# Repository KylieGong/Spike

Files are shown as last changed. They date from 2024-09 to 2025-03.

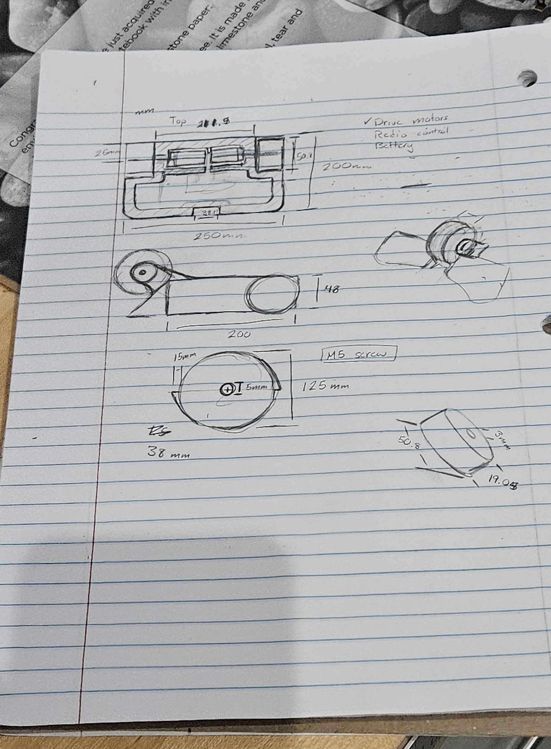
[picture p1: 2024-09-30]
Sketches/dim_drawings.jpg

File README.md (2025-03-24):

# Spike
Spike is a 1lb combat robot designed to participate at the competition known 
as 

**SCR@M**: https://leatherbacks.notion.site/SCR-M-Allowed-Parts-List-7415e14e8c94436496a05054f4add28d

This event was organized by the combat robotics club **Leatherbacks Combat Robotics** 

Instagram profile: https://www.instagram.com/leatherbacks.umd/

## Type of robot
Spike is a vertical spinner robot with two teeths and guards attached to the front so it can break in half whoever stands in its way. 
It's body structure was made of PLA with about 15% in-fill on average.

## Part List
See document attached bill of materials.csv

## CAD Design 
The software used was Solidworks 2024 Student Edition
### First Version


### Spike last version


## Ready before fight


## Fight!



https://photos.app.goo.gl/Wb8rTZ4aMuBoXnDs7

## After fight 


## Future improvements 
- Change the way the weapon mounts are attached.
- Determine a better attack angle for the spinner.
- Check zones that can be reduced without pushing the electrical wiring and components inside. 
- Try new ideas for fastening.
- Design a different geometry for the saw.

## Lessons Learned
- Tolerances are crucial to achieve some design requirements. 
- Measure every component if available so less corrections are required.
- Look for the simple ways to fasten and assembly together components. 
- In real there's always fixes on  we can do at the cost of performance (eg: plastic welding)

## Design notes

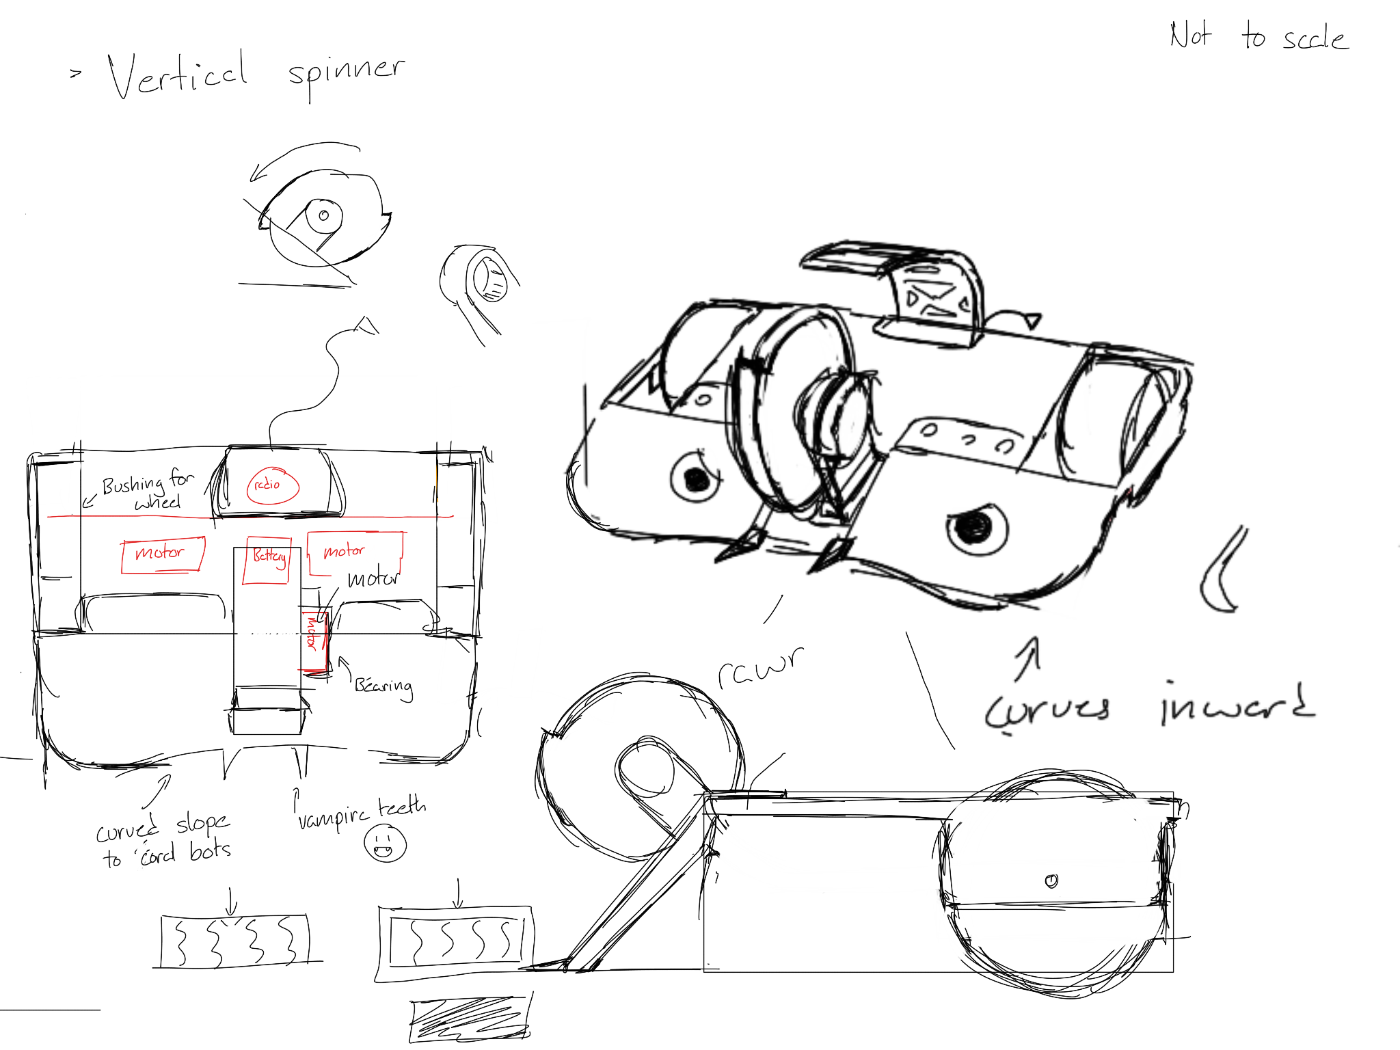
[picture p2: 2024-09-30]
Sketches/design.png

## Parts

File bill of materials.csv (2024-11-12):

ITEM NO. | PART NUMBER | DESCRIPTION | LINK | QTY.
1 | chassie v4 | Body spike | N/A | 1
2 | motor drive mount | PLA | N/A | 2
3 | cover plate | PLA | N/A | 1
4 | weapon mini | PLA 100% infill | N/A | 1
5 | weapon mount 1 | PLA | N/A | 1
6 | weapon mount 2 | PLA | N/A | 1
7 | teeth armor | PLA | N/A | 1
8 | wheels | 2x0.75in foam wheels | https://www.fingertechrobotics.com/proddetail.php?prod=ft-foam-wheels | 2
9 | battery with cables | Gaoneng GNB 11.4V 3S 380mAh 90C LiHV Micro Battery - XT30 | https://www.racedayquads.com/products/gaoneng-gnb-11-4v-3s-380mah-90c-lihv-micro-battery-xt30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 | 1
10 | FingerTech_Silver_Spark_11 | 16mm shaft | https://www.fingertechrobotics.com/proddetail.php?prod=ft-Sspark16 | 2
11 | Lite_Hub | Lite hubs for wheels | https://www.fingertechrobotics.com/proddetail.php?prod=ft-lite-hubs | 2
12 | mini power switch | Fingertech mini power switch | https://www.fingertechrobotics.com/proddetail.php?prod=ft-mini-switch | 1
13 | ESC Motor drive | Budget Ant DESC | https://repeat-robotics.com/buy/desc/ | 2
14 | ESC weapon | Flycolor Raptor 5 BLHeli_32 3-6S DShot 1200 35A ESC | https://www.getfpv.com/flycolor-x-cross-blheli-32-35a-3-6s-dshot-1200-esc.html | 1
15 | Radiomaster R84 | ER4 2.4GHz ELRS PWM Receiver | https://www.radiomasterrc.com/products/er4-2-4ghz-elrs-pwm-receiver | 1
16 | 2207 motor | TMOTOR Velox V2207 V3 Brushless Drone Motor | https://shop.tmotor.com/products/tmotor-velox-v2207-v3-motor | 1
17 | 5972K197 | Ball Bearing 5mm | https://www.mcmaster.com/products/bearings/ball-bearings~/ball-bearings-8/shaft-diameter~5-mm/ | 1
18 | 91290A115 | Alloy Steel Socket Head Screw | https://www.mcmaster.com/catalog/130/3544/91290A115 | 12
19 | 91290A117 | Alloy Steel Socket Head Screw | https://www.mcmaster.com/catalog/130/3544/91290A119 | 4
20 | 91290A123 | Alloy Steel Socket Head Screw | https://www.mcmaster.com/catalog/130/3544/91290A123 | 4
21 | 2-56 Button head screws | Button Socket Cap Screw: #2-56 3/16" Length Under Head Alloy Steel Black Oxide | https://www.fingertechrobotics.com/proddetail.php?prod=screw256BH-25pcs | 4
22 | Head inserts | Brass Tapping Inserts for Plastic | https://www.amazon.com/Threaded-Inserts-Printing-Embedment-Automotive/dp/B0BQJ6CRNJ | 16

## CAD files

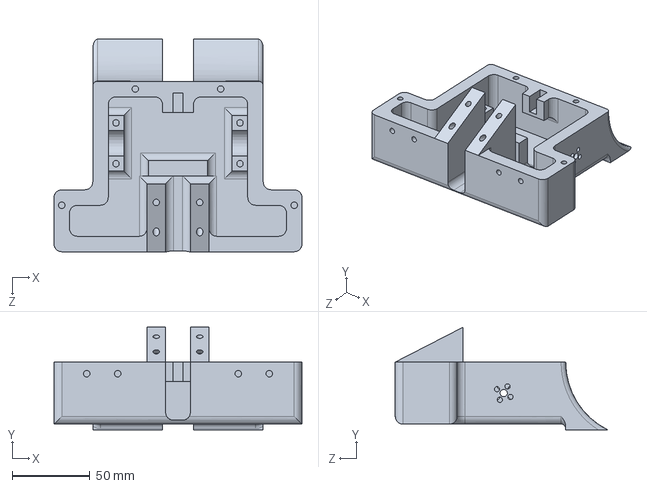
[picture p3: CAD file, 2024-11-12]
CAD/chassis_v4.SLDPRT
160.0 x 66.2 x 137.1 mm

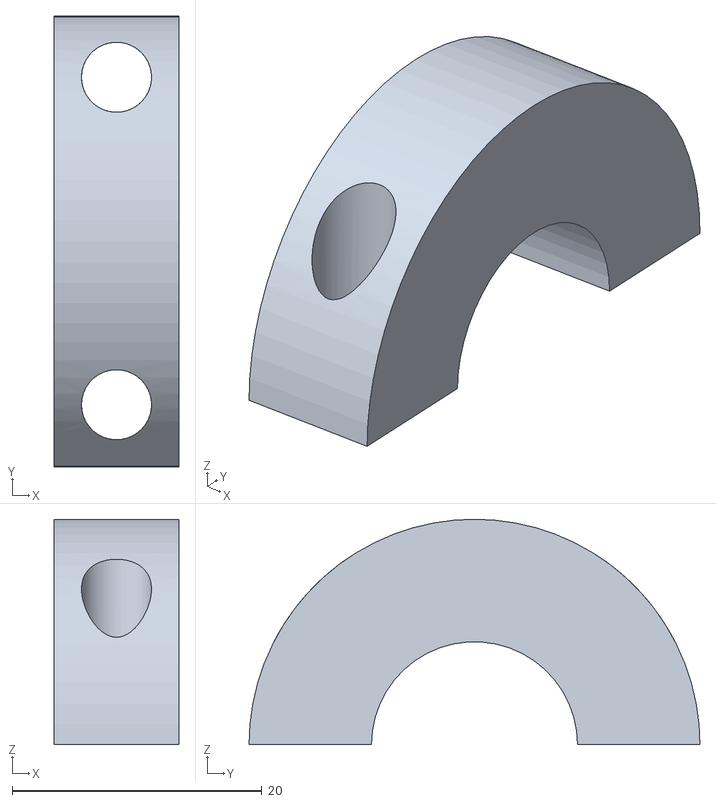
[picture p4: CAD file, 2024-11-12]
Parts to print/motor drive mount up-PLA-2X.STL
10.0 x 36.1 x 18.0

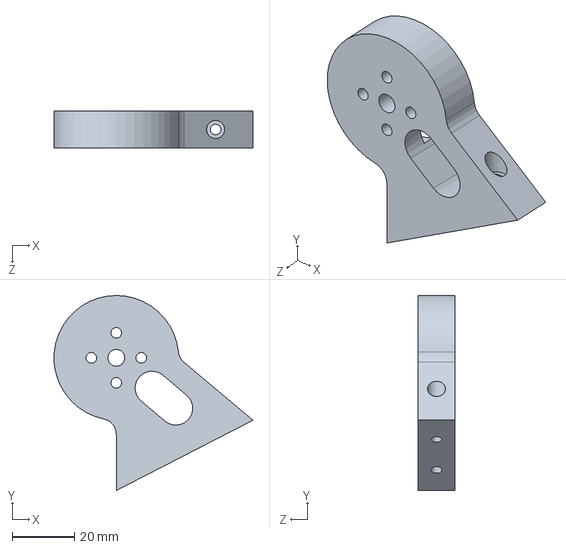
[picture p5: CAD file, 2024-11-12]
CAD/mount for weapon part1.SLDPRT
63.8 x 62.5 x 12.0 mm

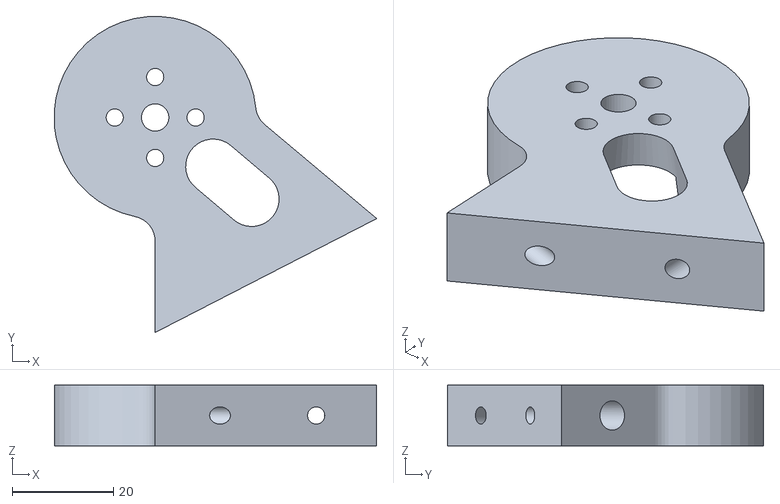
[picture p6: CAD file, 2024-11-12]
Parts to print/mount weapon1-PLA-1X.STL
63.8 x 62.5 x 12.0

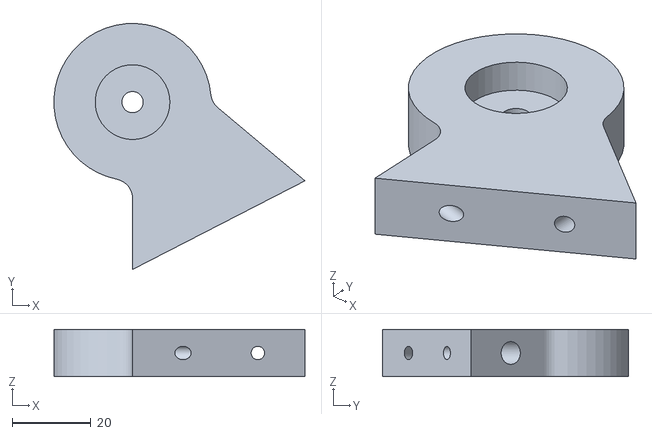
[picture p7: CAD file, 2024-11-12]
Parts to print/mount weapon2-PLA-1X.STL
63.8 x 62.5 x 12.0

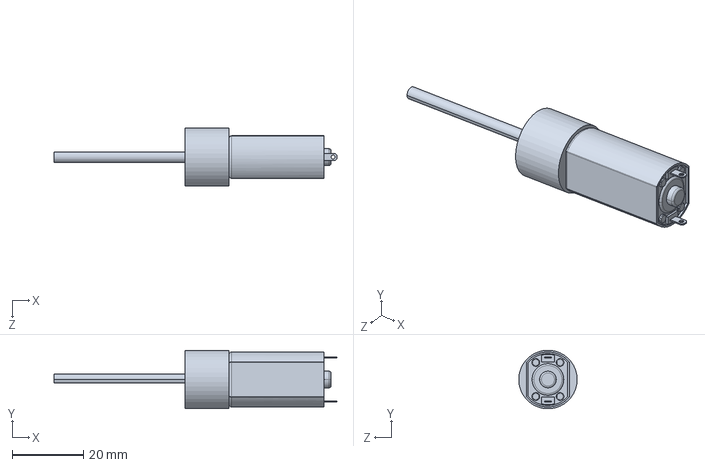
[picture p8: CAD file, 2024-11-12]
CAD/FingerTech_Silver_Spark_223350.SLDPRT
79.7 x 16.5 x 16.5 mm

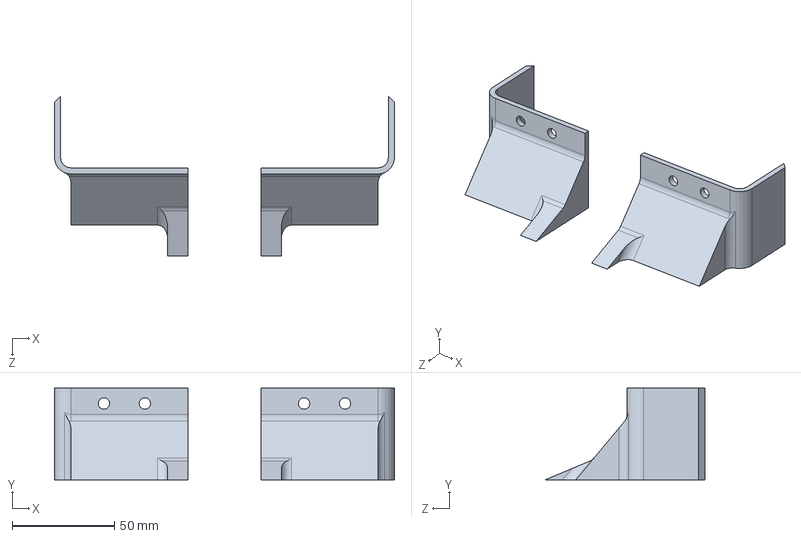
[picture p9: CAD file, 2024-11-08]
CAD/wedge teeth.SLDPRT
166.0 x 44.8 x 78.0 mm

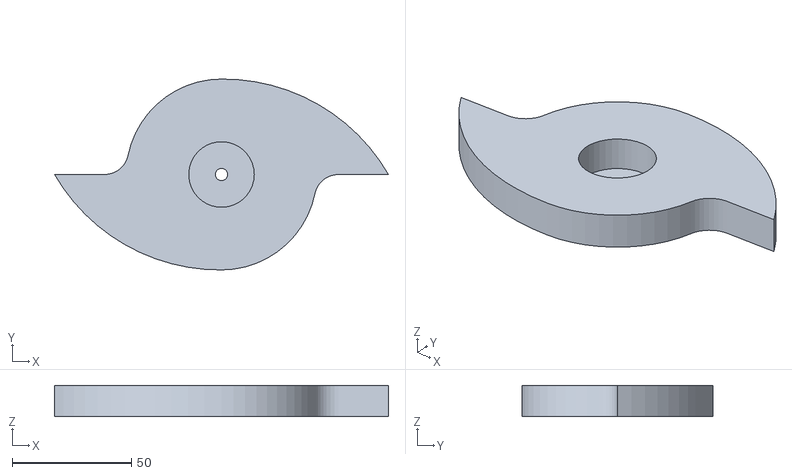
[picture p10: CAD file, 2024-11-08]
Parts to print/weapon-PLA-1X-100% infill.STL
140.0 x 80.0 x 13.0

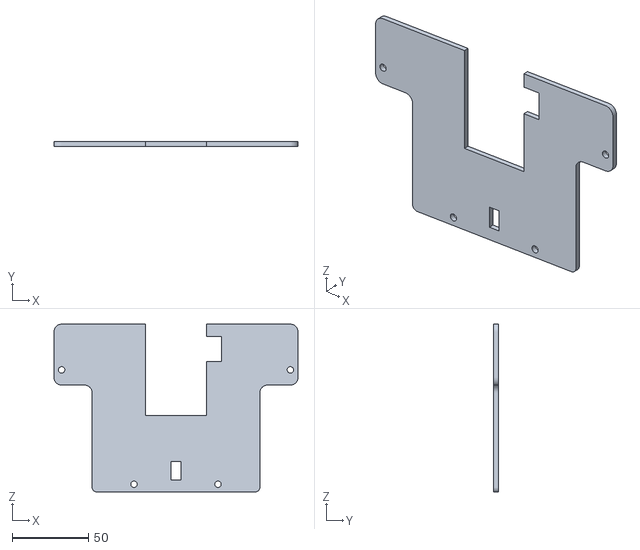
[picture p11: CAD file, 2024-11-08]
Parts to print/cover plate-PLA-1X.STL
160.0 x 3.00 x 110.0

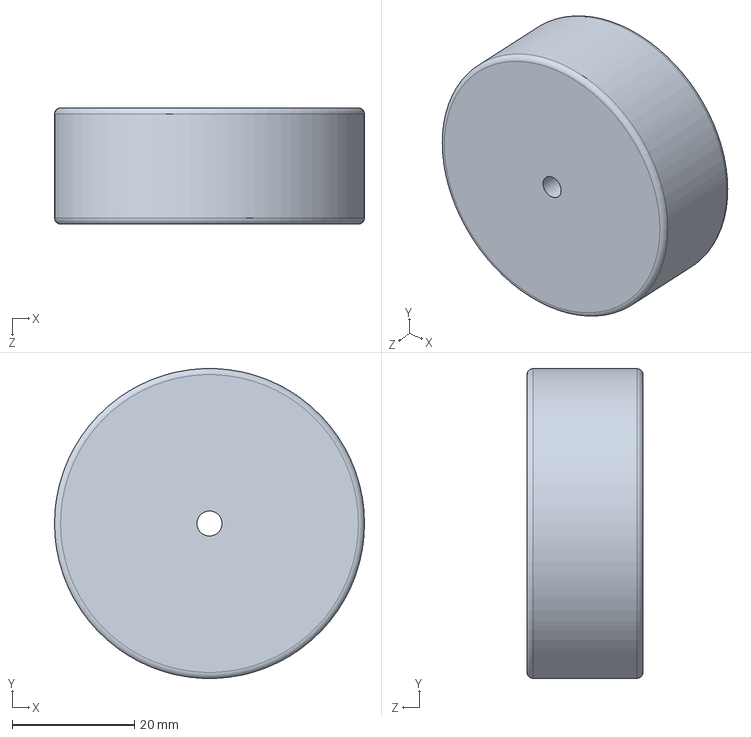
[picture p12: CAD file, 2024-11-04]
CAD/wheels.SLDPRT
50.8 x 50.8 x 19.1 mm

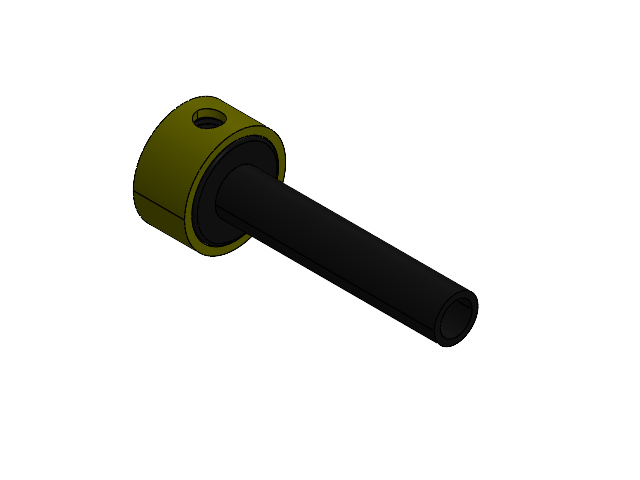
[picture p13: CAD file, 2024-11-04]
CAD/Lite_Hub.SLDASM
Lite hubs.IGS
Hub Sleeve R2.IGS

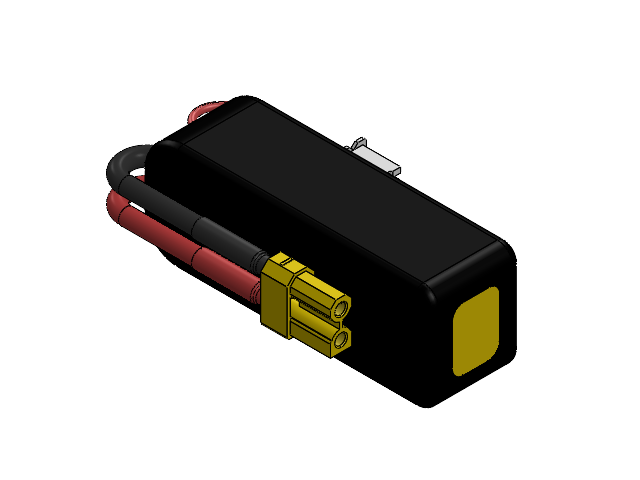
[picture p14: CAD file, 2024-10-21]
CAD/battery with cables.SLDASM
16GA (XT30) v1 (1).step
Heat Shrink (1).step
16GA (XT30).step
XT30 Wire-0.step
Label (1).step
Cells.step
Wrap.step
XHP-4 3S Balance Lead.step

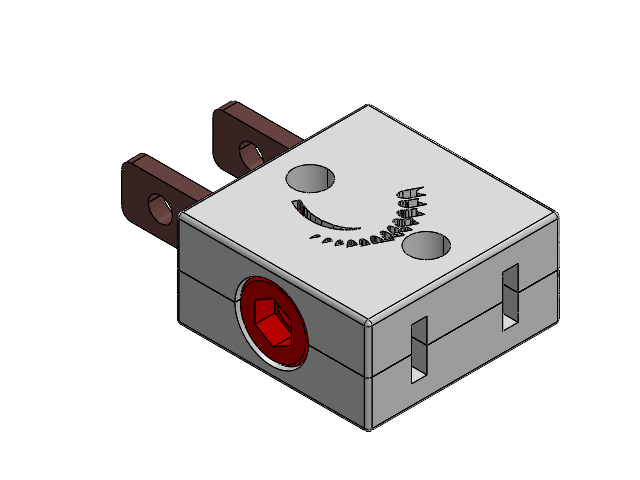
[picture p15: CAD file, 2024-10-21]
CAD/mini power switch.SLDASM
switch half R1.1.IGS x 2
copper tab_through hole.IGS
copper tab.IGS
SHCS 4-40x375_HX-SHCS 0.112-40x0.375x0.375-S.IGS

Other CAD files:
CAD/motor mount upper.SLDPRT
Parts to print/chassis-PLA-1X.STL
Parts to print/wedge teeth-PLA-1X.STL
CAD/mount for weapon part 1 two.SLDPRT
CAD/cover plate.SLDPRT
CAD/2-56 3_16 Button Socket Cap Screw.SLDASM
CAD/5mm bearing.SLDPRT
CAD/91290A113_Alloy Steel Socket Head Screw.SLDPRT
CAD/91290A115_Alloy Steel Socket Head Screw.SLDPRT
CAD/91290A117_Alloy Steel Socket Head Screw.SLDPRT
CAD/91290A123_Alloy Steel Socket Head Screw.SLDPRT
CAD/93722A211_Brass Tapping Inserts for Plastic.SLDPRT
CAD/ESC Motor drive.SLDPRT
CAD/ESC weapon.SLDPRT
CAD/Radiomaster R84.SLDPRT
CAD/Weapon design.SLDPRT

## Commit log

2024-09-30 added sketches and cad files (assembly+wheel)
    [wheel.SLDPRT]
2024-10-07 new rf, changed wheel diameter and added to asemble
    [Radiomaster R84.SLDPRT]
2024-10-08 modifications to weapon and mounting as well, added 5 mm bearing
    [5mm bearing.SLDPRT, weapon mini 1.SLDPRT, weapon mini 2.SLDPRT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]
2024-10-11 changes to the chassis to assembly the weapon, change of mounting weapon, minor fixes
    [chassie v2.SLDPRT, weapon mini 1.SLDPRT, weapon mini 2.SLDPRT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]
2024-10-15 Create main assembly
    this is the current designs of the bot, please notify the group if you are making significant changes
2024-10-15 Add files via upload
    has drill holes for arm on main body and motor mounts, does not have a lid and stop gap for electronics
2024-10-15 cad files for fasteners, mini power switch ,wheels cad modification
    [Nut M3_0.5mm width_5_5mm height_2_4mm.SLDPRT, chassie.SLDPRT, head flat screw M3X0_5mm length_12mm.SLDPRT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]
2024-10-20 Full first correct assembly, design of cover plates, modification to the design, remove of old non functional files, correction of dimensions, missing add fasteners
    [ESC Motor drive.SLDPRT, ESC weapon.SLDPRT, FingerTech_Silver_Spark_11.SLDPRT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]
2024-10-21 added fasteners and created bill of materials, settled pieces to 3d printing, minor changes
    [2-56 3_16 Button Socket Cap Screw.SLDASM, 5mm bearing.SLDPRT, 91290A113_Alloy Steel Socket Head Screw.SLDPRT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]
2024-11-04 spike v4, pending improve weapon mount
    [91290A115_Alloy Steel Socket Head Screw.SLDPRT, 93722A211_Brass Tapping Inserts for Plastic.SLDPRT, Chassis Spike - PLA - 1x -100% infill.SLDPRT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]
2024-11-08 Spike V5, added threaded inserts, resize of the vehicle,separate teeth and armor, weapon mount is now dettachable
    [91290A115_Alloy Steel Socket Head Screw.SLDPRT, 91290A117_Alloy Steel Socket Head Screw.SLDPRT, 91290A119_Alloy Steel Socket Head Screw.SLDPRT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]
2024-11-12 added tolerance for motor drive mount and guard, changed the motor cad
    [FingerTech_Silver_Spark_11.SLDPRT, FingerTech_Silver_Spark_223350.SLDPRT, bill of materials.csv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]
